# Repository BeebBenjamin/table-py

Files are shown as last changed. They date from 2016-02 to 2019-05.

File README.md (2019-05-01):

<h1> Introduction to table-py</h2>
<p align="justify">table-py is a Python (2.7) wrapper and Arduino UNO driver for a Lego based or completely 3D printable photogrammetry machine!  The setup is basically a stepper motor driven by an Adafruit v1.0 or v2.0 motor shield; attached to an Arduino UNO and connected by serial/USB to a PC.  The wrapper is for utilising the program gphoto2 in order to control a digital SLR, which takes a picture of an object placed on the turn-table and then tells the motor to step via the Arduino.  In this way, a user can take pictures of a object around a fixed point for later use in photogrammetry software in order to build a 3D model of the chosen object.  Such a set up is useful as it frees up the user from having to aim the camera, or move the object themselves, potentially saving both time and improving overall consistency.</p>

<h2>Build Instructions (for the actual machine)</h2>
<p align="justify">Build instructions for the Lego machine are not available, however, the Lego Digital Designer file is included <a href="https://github.com/BeebBenjamin/table-py/blob/master/parts/lego%20parts/turn-table-m3.lxf">here</a> and can therefore be reverse engineered using Lego Digital Designer (available from www.Lego.com).  A BOM can also be found in this repository on GitHub <a href="https://github.com/BeebBenjamin/table-py/edit/master/BOM.xlsx">here</a>.</p>

<h2>Software</h2>
table-py consists of a python wrapper and Arduino firmware that makes use of a number of third party libraries, modules, and programs that need to be installed on your computer for it to work correctly and these are listed below:

<h3>Arduino Libraries</h3>

AFMotor.h (library) obtained from GitHub <a href="https://github.com/adafruit/Adafruit-Motor-Shield-library/zipball/master">here</a>.

<h3>Third Party Python Modules</h3>

pyserial (pip install pyserial) or from GitHub <a href="https://github.com/pyserial/pyserial/zipball/master">here</a>.

<h3>External Programs</h3>

gphoto2 (program) obtained through apt (Advanced Package Tool) for Linux or from GitHub
<a href="https://github.com/gphoto/gphoto2/zipball/master">here</a>.  It can be a real pain getting things like this onto a Mac, however, gphoto may be available through 'Macports'.

<h2>Instructions of Use</h2>

Once you have built the machine and have all of these packages/libraries installed follow the instructions below in order to control your setup!

<p align="justify">Using the Ardunio IDE (after you have installed the AFMotor library) copy and paste the code in table-py.ino into the code window and save with whatever name you like.  Then with your Ardunio board (UNO) connected via a USB cable press upload.  You shouldn't get any error messages if you have the required library installed.  To test it's working you can open the serial monitor and type a 'M' this should tell the firmware to make one step.  The motor will step once and hold until you type an 'N' into the serial monitor (to release the motor).  <b>N.B. if you do not release the motor after testing you wont be able to turn it manually and the motor may get hot.</b></p>

<p align="justify">Next attach you digital SLR camera via a USB cable and unmount it if using Linux, on a Mac this is done in the terminal using the command "killall PTPCamera".  N.B. I have only tested this with a Canon EOS 30D and a Nikon D5100 on Ubuntu/OSx and would appreciate feedback on another camera/OS.  I do know that cameras which are PTP only e.g. Canon Powershot cameras etc may not work properly with gphoto2 using their native firmware and an alternative program using CHDK and the PTP extension needs to be used.  As such my current setup won't work for you. Yet.  A list of cameras supported by gphoto2 can be found <a href="http://gphoto.sourceforge.net/proj/libgphoto2/support.php">here</a>.</p>

<p align="justify">If you have installed the pyserial module and Python 2.7 and have your Python path set correctly (particularly an issue in Windows) then you can browse to where your python script is located using the terminal and type the following command: "python table-py.py" in order to run the turn-table "in default mode" (camera active and the motor will step 35 times taking 35 pictures).  Please note that it is possible to make use of the following "flags" inorder to change those default settings:  

"--o" (override) will allow you to enter a user defined number of times you wish the table to turn and take a photo.

"--c" (camera off) will allow you to turn off gphoto2 and just make use of the turn-table, should you so wish.

These flags are entered as follows: python table-py.py --o --c in any combination depending on what you want to do.

The user will also be asked before the run to define a custom name to label photos with, if you care about this sort of thing (if nothing is entered table-py will use the camera defaults).  If all goes well, the camera will take a test photo and the table will turn and take a photo the number of times specified.  Then at the end of the run the photos will be transfered to the directory the script is running from with the user specified labels.</p>

<h2>Troubleshooting</h2>

<h3>Camera specific Issues</h3>

Here are some things to check out if you get the "There seems to be an issue communicating with your camera" error. 

1. Check the camera is unmounted.

2. Check the USB is plugged in.

3. Check that the battery is working and charged.

4. Check your camera model is compatible with gphoto2.

Some cameras need to have "Normal" or "PC communication" activated and not "Print/PTP" in order to work with gphoto2.

<h3>Arduino Issues</h3>

<p align="justify">If the motor doesn't step check which motor slot it is attached to.  The firmware specifies "M4" of the Adafruit v1.2 motor shield as the default.  You may change this if you want to.</p>

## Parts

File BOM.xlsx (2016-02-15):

Brick | Name | Picture | Part | Color code | Quantity | Official | Official subs | Third Party | Third Party Subs
300401 | BRICK 1X2 |  | 3004 | 1 - White | 3 | 0.09 | 0.27 | 0.005 | 0.00135
362201 | BRICK 1X3 |  | 3622 | 1 - White | 5 | 0.12 | 0.6 | 0.01 | 0.006
300301 | BRICK 2X2 |  | 3003 | 1 - White | 7 | 0.12 | 0.84 | 0.005 | 0.0042
301001 | BRICK 1X4 |  | 3010 | 1 - White | 5 | 0.12 | 0.6 | 0.0069 | 0.00414
300201 | BRICK 2X3 |  | 3002 | 1 - White | 2 | 0.15 | 0.3 | 0.008 | 0.0024
300901 | BRICK 1X6 |  | 3009 | 1 - White | 2 | 0.21 | 0.42 | 0.02 | 0.0084
300101 | BRICK 2X4 |  | 3001 | 1 - White | 7 | 0.18 | 1.26 | 0.01 | 0.0126
4211526 | BRICK Ø16 W. CROSS |  | 6143 | 194 - Medium Stone Grey | 4 | 0.18 | 0.72 | 0.005 | 0.0036
4558168 | FLAT TILE 1X3 |  | 63864 | 1 - White | 1 | 0.12 | 0.12 | 0.02 | 0.0024
362301 | PLATE 1X3 |  | 3623 | 1 - White | 1 | 0.06 | 0.06 | 0.01 | 0.0006
303426 | PLATE 2X8 |  | 3034 | 26 - Black | 2 | 0.21 | 0.42 | 0.01 | 0.0042
383226 | PLATE 2X10 |  | 3832 | 26 - Black | 4 | 0.21 | 0.84 | 0.02 | 0.0168
244526 | PLATE 2X12 |  | 2445 | 26 - Black | 3 | 0.24 | 0.72 | 0.03 | 0.0216
303326 | PLATE 6X10 |  | 3033 | 26 - Black | 4 | 0.73 | 2.92 | 0.02 | 0.0584
4142969 | TECHNIC 7M BEAM |  | 32524 | 1 - White | 2 | 0.18 | 0.36 | 0.02 | 0.0072
4156341 | TECHNIC 9M BEAM |  | 64289 | 1 – Black | 4 | 0.3 | 1.2 | 0.03 | 0.036
3252501 | TECHNIC 11M BEAM |  | 32525 | 1 - White | 2 | 0.21 | 0.42 | 0.06 | 0.0252
4211573 | 1/2 BUSH |  | 32123 | 194 - Medium Stone Grey | 4 | 0.06 | 0.24 | 0.004 | 0.00096
4211483 | CONNECTOR PEG W. KNOB |  | 4274 | 194 - Medium Stone Grey | 5 | 0.09 | 0.45 | 0.0008 | 0.00036
4142865 | 2M CROSS AXLE W. GROOVE |  | 32062 | 21 - Bright Red | 2 | 0.06 | 0.12 | 0.0033 | 0.000396
278026 | CONNECTOR PEG W. FRICTION |  | 2780 | 26 - Black | 8 | 0.06 | 0.48 | 0.0034 | 0.001632
4516546 | CROSS AXLE, EXTENSION, 2M |  | 59443 | 199 - Dark Stone Grey | 1 | 0.05 | 0.05 | 0.0069 | 0.000345
4512360 | CROSS AXLE, EXTENSION, 2M |  | 59443 | 194 - Medium Stone Grey | 4 | 0.05 | 0.2 | 0.0069 | 0.00138
4211086 | CROSSAXLE 3M WITH KNOB |  | 6587 | 199 - Dark Stone Grey | 5 | 0.14 | 0.7 | 0.0069 | 0.00483
370726 | CROSS AXLE 8M |  | 3707 | 26 - Black | 2 | 0.12 | 0.24 | 0.01 | 0.0024
4225033 | BEAM 3 M. W/4 SNAPS |  | 48989 | 194 - Medium Stone Grey | 2 | 0 | 0 | 0.03 | 0
4296059 | Angular beam 90degr. w.4 snaps |  | 55615 | 194 - Medium Stone Grey | 4 | 0.4 | 1.6 | 0.27 | 0.432
4514558 | GEAR WHEEL Z24 |  | 3648 | 199 - Dark Stone Grey | 1 | 0.34 | 0.34 | 0.02 | 0.0068
4235858 | TURNTABLE 4.85 |  | 50163 | 26 - Black, 199 - Dark Stone Grey | 1 | 1.49 | 1.49 | 0.81 | 1.2069
 |  |  |  | Total pieces | 97 | Official | £17.98 | Third Party | £1.87
N.B. red background indicates that this item is either not available through the Lego 'pick a brick' or 'bricks and pieces' service.
The pricing for third party Lego pieces is the minimum price on offer as of the 15/02/2016 as found on www.bricklink.com and therefore cannot be guaranteed.
Other Items
Lego MK-3 Build
Name | Part | Supplier | Official Unit Price | Clone Unit Price | Units | Official Subs | Clone Subs
Genuino Uno | - | Pimoroni | 18.5 | 9.73 | 1 | 18.5 | 9.73
Adafruit Motor Shield v1.0 or v2.0 | - | Pimoroni | 18 | 5.23 | 1 | 18 | 5.23
0.6A variable (12v) power supply | ES1340 | Amazon | 7.86 | 7.86 | 1 | 7.86 | 7.86
5v Stepper Motor | 28BYJ-48 | Adafruit | 2 | 2 | 1 | 2 | 2
3D printed turn-table adaptor | - | 3D Printing | 4 | 4 | 1 | 4 | 4
3D printed stepper motor adaptor | - | 3D Printing | 2 | 2 | 1 | 2 | 2
 |  |  |  |  | Totals | 52.36 | 30.82
NEMA MK-1 Build
Name | Part | Supplier | Official Unit Price | Clone Unit Price | Units | Official Subs | Clone Subs
Genuino Uno | - | Pimoroni | 18.5 | 9.73 | 1 | 18.5 | 9.73
Adafruit Motor Shield v1.0 or v2.0 | - | Pimoroni | 18 | 5.23 | 1 | 18 | 5.23
0.6A variable (12v) power supply | ES1340 | Amazon | 7.86 | 7.86 | 1 | 7.86 | 7.86
NEMA-17 Stepper Motor (12v 350mA) | - | PiSupply | 13 | 13 | 1 | 13 | 13
3D Printed Parts (top and base) | - | 3D Printing | 6 | 6 | 1 | 6 | 6
Lego Pin | 2780 | Lego | 0.06 | 0.003 | 2 | 0.12 | 0.006
 |  |  |  |  | Totals | 63.48 | 41.826
N.B. costs are subject to deals and if bought second hand. The prices listed here make the assumption that parts are either bought new or are non official clones of the originals listed.
Part numbers are not needed as the vendors use key words. Again prices or availability for any parts cannot be guaranteed.
Total for Lego MK-3 Build
Official | Clone/Thirdparty
£70.34 | £32.69
Total for NEMA MK-1 Build
Official | Clone/Thirdparty
63.48 | 41.826

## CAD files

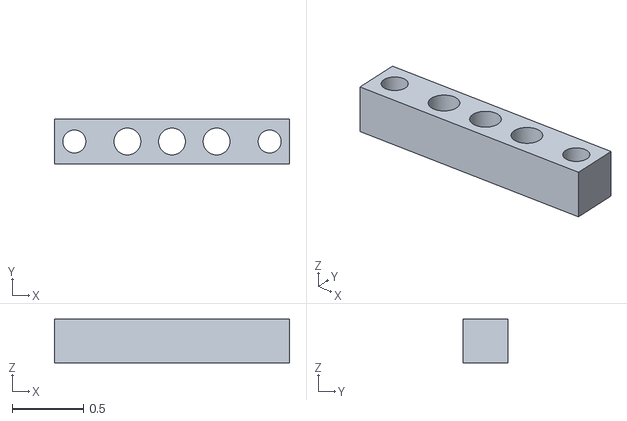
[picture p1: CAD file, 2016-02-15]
parts/3d printable parts/Lego MK-3/5v-motor-adaptor.stl
1.65 x 0.315 x 0.307

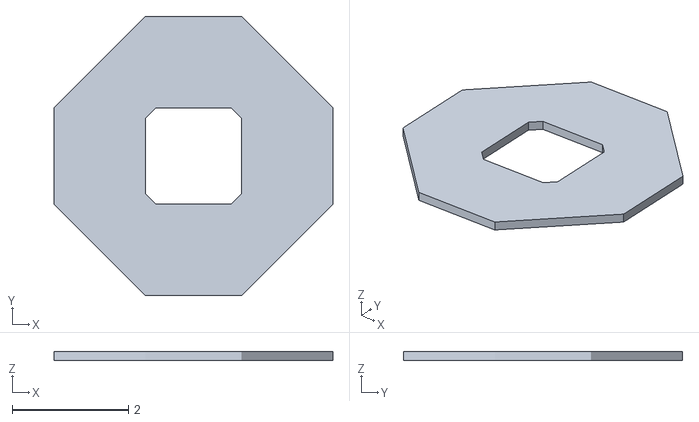
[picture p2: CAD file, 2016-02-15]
parts/3d printable parts/NEMA MK-1/turn-table-nema-base.stl
4.80 x 4.80 x 0.157

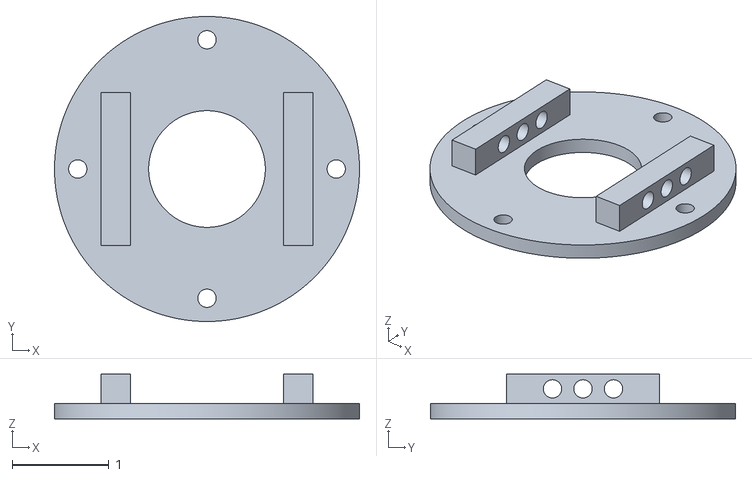
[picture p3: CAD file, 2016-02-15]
parts/3d printable parts/Lego MK-3/lego-turn-table-adaptor.stl
3.15 x 3.15 x 0.465

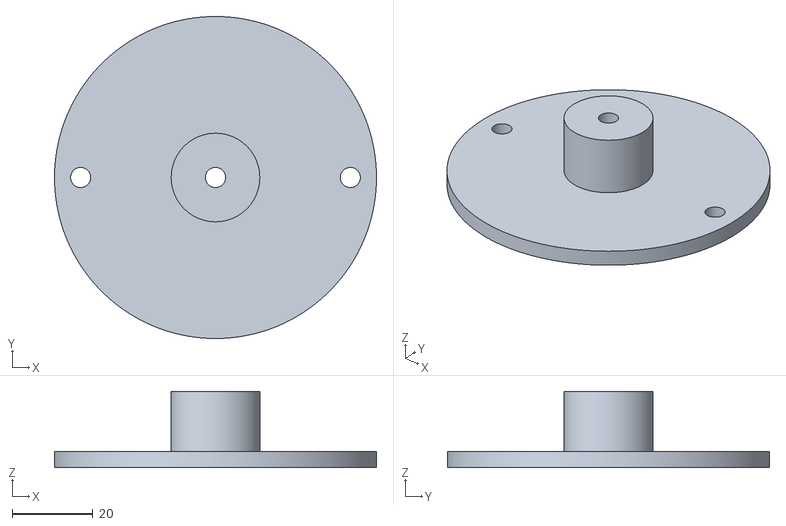
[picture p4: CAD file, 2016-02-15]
parts/3d printable parts/NEMA MK-1/turn-table-nema-top.stl
80.0 x 80.0 x 19.0

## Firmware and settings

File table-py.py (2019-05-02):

#!/usr/bin/python2
"""
    Todo: 
        make the nested ifs more human readable by moving them to functions
"""
# import all python 2.7 native modules
import serial
import sys
import os
import subprocess
import time
import atexit

# import SerialException class from non-native module: serial
from serial import SerialException


def exit_handler(serial_name):
    """In the event of the user interrupting the program using a 'ctrl + c' command
       or 'keyboard interrupt', this function will attempt to send the off command
       'N' to the arduino in order to switch off the motors and give feedback to the
       user if the off command was written to the USB serial port.

       Args:
                    serial_name (str): The name of the serial port as defined in main()

       Returns:
                    N/A
    """
    # define a serial object using serial_name and connect at the baud rate in use by the arduino
    ser = serial.Serial(serial_name, 9600)
    # write an 'N' character to the serial buffer
    ser.write('N')

    # print a message to the terminal telling the user the program is now closing
    print "\n\nApplication terminating, closing down motor, Goodbye!\n"


def main():
    # try until user uses a keyboard interrupt
    try:
        # register the exit_handler function to exit event
        atexit.register(exit_handler)

        # serial name will be different for a Mac or Linux/GNU
        serial_name = "/dev/cu.usbmodem1411"  # set for Mac

        # define working directory by grabbing the path of the current script
        # can be changed to something like '/home/user/Documents/subfolder' but currently just grabs the directory the python script is in!
        working_directory = sys.path[0]

        # try establishing a serial connection
        try:
            # define serial using name grabbed above
            ser = serial.Serial(serial_name, 9600)

            # look for flags passed as arguments in the system command line
            options = sys.argv

            # if there is an override '--o' flag then the user will be prompted for the custom number of steps they want the table to make, it's usually around 35 per turn.
            if "--o" in options:

                # loop until user gives correct answer
                while True:
                    # ask user to define how many pictures they need per 360 degs via the terminal
                    iterations = raw_input(
                        "\nHow many iterations do you need? ")

                    # try to convert the answer given by the user to a integer
                    try:
                        iterations = int(iterations)
                        break

                    # if variable isnt convertable to an integer ask again for correct input
                    except:
                        print "\nThis is not an integer (whole number), please type in an integer value!\n"

            # otherwise use the default value.
            else:
                iterations = 38

            # if there is an override '--c' flag then the user will be prompted for the number of seconds they want the delay to be between each step and photo.  The camera will turn off and the table will just turn with the object on.
            if "--c" in options:
                # do not use the camera
                camera_override = True

                # loop until user gives correct answer
                while True:
                    # ask user to define how many seconds they want to wait between each step (to simulate presence of a camera)
                    time_interval = raw_input("\nHow many seconds would you like inbetween each step? ")

                    # try to convert the answer given by the user to a integer
                    try:
                        time_interval = int(time_interval)
                        break

                    # if variable isnt convertable to an integer ask again for correct input
                    except:
                        print "\nThis is not an integer (whole number), please type in an integer value!\n"

            # otherwise assume a camera is attached!
            else:
                # loop until user gives correct answer re: institution ID
                while True:

                    # loop until user gives correct answer re: motor type
                    while True:

                        # ask for user to choose between a 5v or a 12v motor by typing a 1 or a 2
                        motor_type = raw_input("\nWhat type of motor are you using (e.g. 1 for 5v, 2 for 12v)? ")

                        # if answer isn't a 1 or a 2 ask again for correct input
                        if motor_type not in ['1', '2']:
                            print "\nPlease select only a '1' or a '2'"
                        else:
                            break

                    # terminal text spacer to make terminal more readable
                    print ""

                    # ask for user to define a unique sample code for each set of photos
                    institution_ID = raw_input("What is the institutional code and unique id for this specimen (e.g. NMBE_XXXX)? ")

                    # terminal text spacer to make terminal more readable
                    print ""

                    # ask user to confirm their choice of sample code
                    confirmation = raw_input("Are you sure you wish to use this ID#: " + institution_ID + "?  Type y/n: ")

                    # if the user confirms move on
                    if confirmation == "y":

                        # terminal text spacer to make terminal more readable
                        print ""
                        break

                    # if the user rejects ask for input again
                    elif confirmation == "n":

                        # terminal text spacer to make terminal more readable
                        print ""

                # loop until the user defines if the sample being photographed is the dorsal or ventral side
                while True:

                    # ask user to use a 'd' or a 'v' to select dorsal or ventral
                    position = raw_input("Dorsal or Ventral?  Type d/v: ")

                    # terminal text spacer to make terminal more readable
                    print ""

                    # ask user to confirm their choice of side
                    confirmation = raw_input("Are you sure you want to use this position: " + position + "?  Type y/n: ")

                    # if the user confirms move on
                    if confirmation == "y":

                        # if dorsal selected set position variable to "DORSAL"
                        if position == "d":
                            position = "DORSAL"
                            break

                        # if ventral selected set position variable to "VENTRAL"
                        elif position == "v":

                            position = "VENTRAL"
                            break

                        # if neither dorsal or ventral selected then ask user to reconfirm their input
                        else:
                            print "\n'd' or 'v' has not been selected, please specify ventral or dorsal by following the instructions!\n"

                    # if the user rejects ask for input again
                    elif confirmation == "n":

                        # terminal text spacer to make terminal more readable
                        print ""

                # flag camera as in user
                camera_override = False

                # adjust the timings if you need to here, default is 0 but if the camera is slow, user can set this higher
                time_interval = 0

            # warn the user of the default settings and the override options.
            if "--o" in options and "--c" in options:

                print "\nRunning program with user specified steps and camera overridden!\n"

            elif "--o" in options and "--c" not in options:

                print "\nRunning program with user specified steps and camera active!\n"

            elif "--o" not in options and "--c" in options:

                print "\nRunning program with default steps and camera overridden!\n"

            else:

                print "Running program in default mode: of 35 photos and steps.\n\nIf you require more per revolution include the flag '--o'.\n\nIf you want to turn off the camera include '--c'.\n"

            # define gphoto2 command to capture images
            cmd = ['gphoto2', '--auto-detect', '--capture-image', '--keep']

            # change to true to attempt test image capture at the start of capture
            check = False

            # here the for loop runs three times prompting the user to change camera positions
            for i in range(0, 3):
                for a in range(1, int(iterations)+1):
                    # code to execute in loop only if camera has been overidden using the --c flag
                    if camera_override == True:
                        if motor_type == '1':
                            ser.write('1')
                        elif motor_type == '2':
                            ser.write('2')

                        # pause program for time interval defined earlier
                        time.sleep(time_interval)

                    else:

                        # check for camera errors!  If it can't connect to the camera to take a picture it will
                        if check != True:

                            print "Taking a test image to see if the camera is working!"

                            # attempt to take a picture using gphoto to control the camera
                            try:
                                # use subprocess to run the gphoto2 terminal program shelless and pass it the command list defined above and the working directory
                                subprocess.check_output(
                                    cmd, cwd=working_directory)

                                # terminal text spacer to make terminal more readable
                                print ""

                                print "Camera works, runing through iterations now!\n"

                                # flag check as True once complete so that no more test photos get taken with each loop
                                check = True

                            # if the subprocess fails tell the user and exit the program
                            except:

                                print "/nThere seems to be an issue communicating with your camera, please check it is plugged in, the battery is charged, it is unmounted, and a supported model for gphoto2!\n"

                                break

                        # use subprocess to run the gphoto2 terminal program shelless and pass it the command list defined above and the working directory
                        process = subprocess.Popen(cmd, cwd=working_directory)

                        output = process.communicate()[0]

                        time.sleep(0.25)

                        print output

                        process.wait()

                        # reset proceed variable each iteration
                        proceed = ''

                        # write to the serial port which motor is in use
                        if motor_type == '1':
                            ser.write('1')
                            print str(a) + " Using motor 1"
                        elif motor_type == '2':
                            ser.write('2')
                            print str(a) + " Using motor 2"

                        # wait for the arduino to signal it is done turning by reading the serial port and looking for a 'D'
                        while (proceed != 'D'):
                            proceed = ser.read()
                            print proceed
                            pass

                        print ""

                    # define the last_int variable by grabbing last count of loop
                    last_int = a-1

                # wait for 3 seconds
                time.sleep(3)

                # write an 'N' to the USB serial port to instruct the arudino to turn off the motor
                ser.write('N')

                # wait for the user to confirm if they wish to keep taking photographs and finish 3 rounds at 3 camera angles?
                while True:

                    # if number of rounds is not equal to 3 (index 0) then keep asking user for input each round
                    if i != 2:
                        continue_run = raw_input("Run " + str(i+1) + " of 3 complete, please reposition the camera, type 'y' and enter to confirm or 'n' to cancel and stop the run. ")

                        # check if user has used a 'y' or an 'n'
                        if continue_run != 'y':

                            # if user rejects continue with an 'n' then break loop
                            if continue_run == 'n':
                                print "\nEnding run, continuing with image processing...\n"
                                break

                            # ask user again if answer was not a 'y' or a 'n'
                            else:
                                print "\nPlease type either 'y' or 'n'\n"

                        # if user confirms with a 'y' then break loop
                        elif continue_run == 'y':
                            break
                        else:
                            print "\nPlease type either 'y' or 'n'\n"

                    # if user rejects continue with an 'n' then break loop
                    if continue_run == 'n':
                        break

                    # if number of rounds is equal to 3 (index 0) then break loop
                    if i == 2:
                        print "Run 3 of 3 complete, moving on to image processing!"
                        break
                print ""

            # define gphoto2 command to list files on camera
            cmd = ['gphoto2', '--auto-detect', '--list-files']

            # use subprocess to run the gphoto2 terminal program shelless and pass it the command list defined above and the working directory
            process = subprocess.Popen(
                cmd, cwd=working_directory, stdout=subprocess.PIPE)

            process.wait()

            # define a variable to hold the list of photographs
            files = []

            # iterate through the output of subprocess and append the file names to the files variable
            for line in iter(process.stdout.readline, ''):

                if "#" in line.rstrip():

                    files.append(line.rstrip())

            # define the number of the last picture taken
            last_pic = int(files[-1].split(" ")[0].strip("#"))

            # loop in reverse using number of photos taken and last file number in order to calculate which files to rename and download
            for i in reversed(range(1, last_int+1)):

                # define the gphoto2 command to download a target image to the working directory
                cmd = ['gphoto2', '--auto-detect', "--filename=" + institution_ID +
                       "_" + position + "_" + str(i) + ".jpg", '--get-file', str(last_pic-i)]

                # use subprocess to run the gphoto2 terminal program shelless and pass it the command list defined above and the working directory
                process = subprocess.Popen(cmd, cwd=working_directory)

                process.wait()

            # tell the user that capture is done
            print "Done!"

        # if serial connection fails to initiate tell the user this is what the issue is
        except SerialException:

            print "Port not found, please make sure the arduino is plugged into the USB port!"

    # trigger keyboard interrupt function and shut down the arduino motors
    except KeyboardInterrupt:
        sys.tracebacklimit = 0


# if script is running from this file run main()
if __name__ == "__main__":
    main()

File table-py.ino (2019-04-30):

//import the adafruit motor shield library
#include <AFMotor.h>

//define incomingByte to be used to store a character read from serial port
char incomingByte;

//define the total number of steps for the 5v stepper
double total_steps_1 = 2048; //5v stepper

//define the total number of steps for the 2v stepper
double total_steps_2 = 200;  //12v stepper
 
//define motor port in use
int motor_port_2 = 2;

//define the angle of stepping for the 5v stepper
double angle_1 = 10;

//define the angle of stepping for the 12v stepper
double angle_2 = 10.8;

//define variable to contain number of steps
double number_of_steps = 0; 

//initiate stepper motor conntected to port 2
AF_Stepper stepper_motor_2(total_steps, motor_port_2);

void setup()
{
  //set stepper speed to 5rpm
  stepper_motor_2.setSpeed(5);
 //open serial port connection with a baud rate of 9600 
 Serial.begin(9600);
}
 
void loop()
{
 //select character encoding utf-8
  uint8_t i;

  //if the serial connection works read continuously for incoming characters
  if (Serial.available() > 0) 
  {
    incomingByte = Serial.read();
  }
  else
  {
    //if the incoming character is equal to 1 then step the stepper motor by 10 degrees
    if(incomingByte =='1')
    {
      number_of_steps = angle_1 / (360 / total_steps_1);
      stepper_motor_2.step(number_of_steps, FORWARD,DOUBLE);
      //write a 'D' to the serial port for Python wrapper to read
      Serial.write('D');
      
      //set incomingByte to D to set machine to a 'done' state
      incomingByte ='D';
    }
    //if the incoming character is equal to 1 then step the stepper motor by 10.8 degrees
    if(incomingByte =='2')
    {
      number_of_steps = angle_2 / (360 / total_steps_2);
      stepper_motor_2.step(number_of_steps, FORWARD,DOUBLE);
      //write a 'D' to the serial port for Python wrapper to read
      Serial.write('D');
      
       //set incomingByte to D to set machine to a 'done' state
      incomingByte ='D';
    }
    //if the incoming character is equal to 'N' then turn off the stepper motor and release it
    if(incomingByte =='N')
    {
      stepper_motor_2.release();
    }
  }
}
